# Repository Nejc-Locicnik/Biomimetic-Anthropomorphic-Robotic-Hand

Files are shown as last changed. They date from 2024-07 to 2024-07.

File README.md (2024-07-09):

# Biomimetic Anthropomorphic Robotic Hand

<div style="text-align: center;">
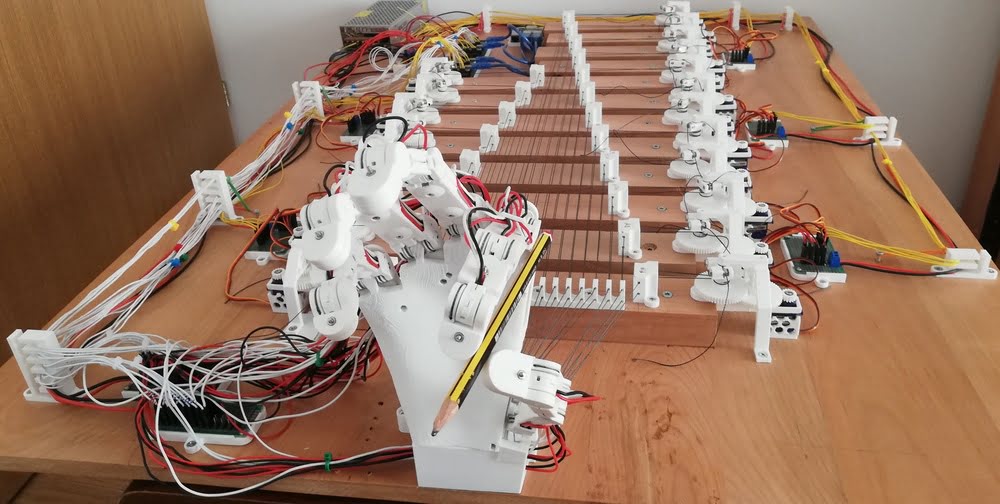
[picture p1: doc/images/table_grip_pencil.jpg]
Cool pic
  
</div>

## Introduction
This repository is a summarization of my diploma thesis, which can be fully read [here](/doc/Biomimetic_Anthropomorphic_Robotic_Hand_Thesis_SLO.pdf). 

The thesis is about designing and manufacturing a working prototype of a 3D printed cable-driven 20-DOF Biomimetic Anthropomorphic Robotic Hand. The main intent was to recreate appropriate hand proportions and joint motions with a simple and modular mechanical structure, which can easily be 3D printed.

## Actuator system

The original idea for moving the joints was to use small "micro" servos in the joints themselves, but I quickly figured that they simply don't provide enough torque to provide consistent motion to the joints (the hand would also become very heavy from the motors and extra cables required). I then pivoted towards cable-driven actuators, where the motors are moved out of the hand entirely. The base cable-pully system was taken from [here](https://www.youtube.com/watch?v=MxbX9iKGd6w&ab_channel=WillCogley). The issue with this system is that moving one joint moves the sequential joint in the opposite direction, I like to call this consequential movement.

I modified the original system by twisting/swapping the cables at specific spots to take advantage of consequential movement to make the finger motion more natural and easier to control. With this change we can actually move all 3 joints of a finger in the same direction with only 1 motor, sadly I figured this out too late and didn't want to modify the rest of the hand. 
The original system and the change are visualized in the following images. The motion is the same in both images (45° flex on each finger joint), but as we can see the final finger position is a lot different:

<div style="text-align: center;">
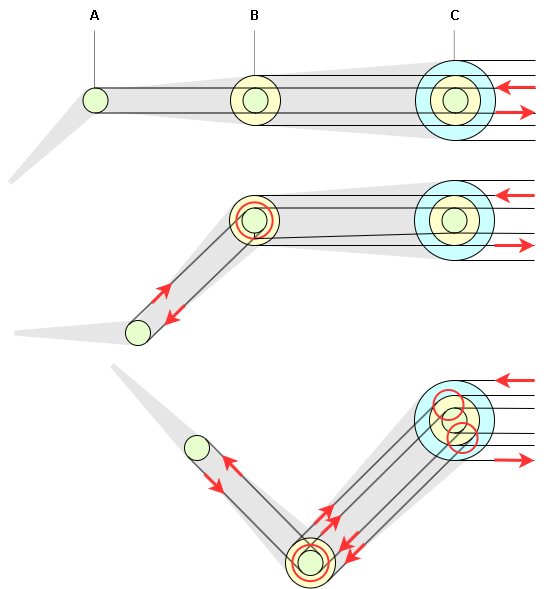
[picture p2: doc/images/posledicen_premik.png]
  
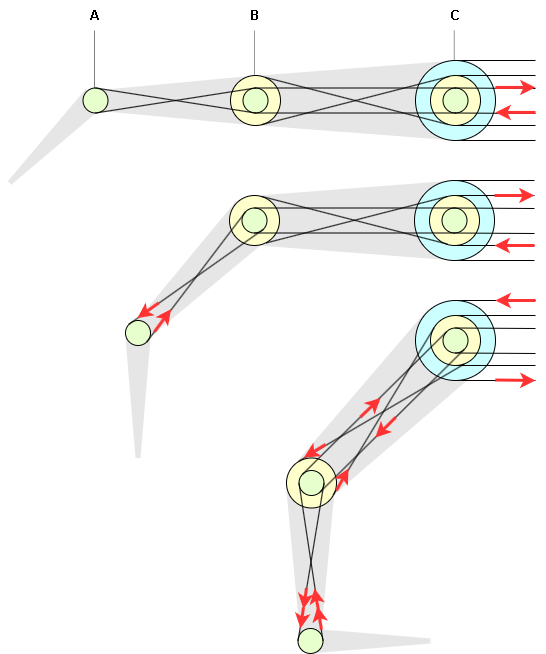
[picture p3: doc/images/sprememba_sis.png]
Modified system Modified system.
  
</div>

Check out the thesis if you are interested in consequential joint movement. I explain (with simple math/geometry) the cause, amount and direction of consequential movement. In my opinion this cable system modification is the most interesting bit of my thesis. 

## 3-D printed parts

All parts were modeled with SolidWorks (2022/2023) and 3D printed with Creality's Ender-5 (slicer used was CURA 5). Everything that could possibly be printed was printed (an extreme example: the joint axis were 3D printed). Most joints (DIP/PIP) are normal hinge joints, while the rest (MCP/CMC) are 2D joints that use a cross axis. All joints require a lot of small bearings.

A large majority of the project's time was spent on designing the robotic hand as I was referencing the actual anatomical structure of a human hand (proportions and the range of motion of each joint).

<div style="text-align: center;">
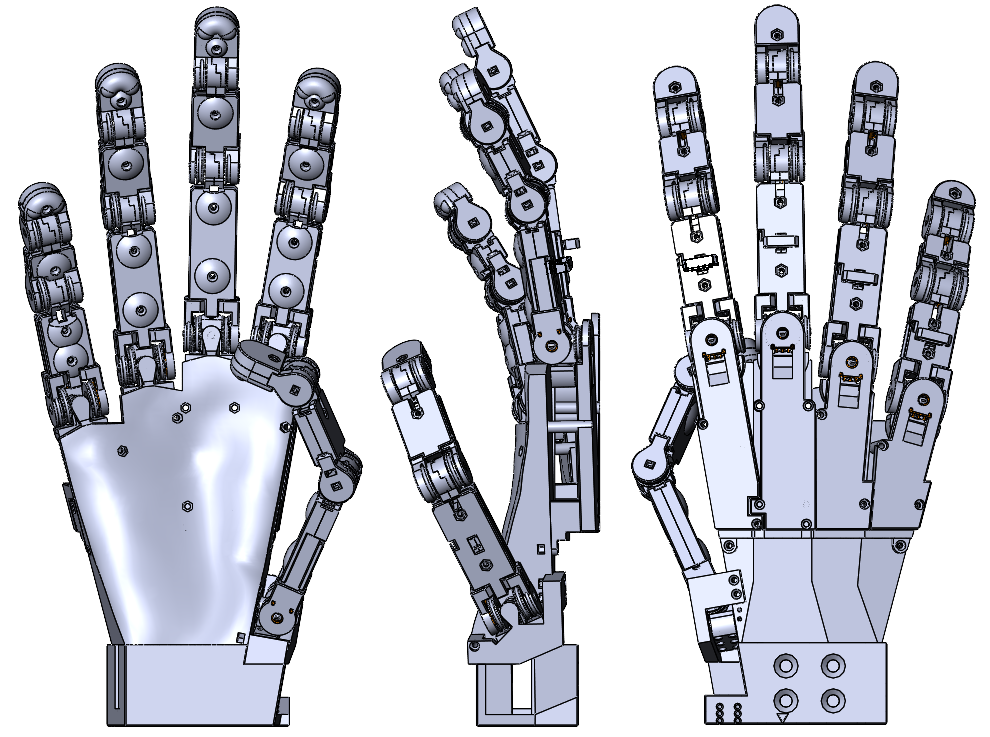
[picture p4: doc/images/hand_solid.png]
  
</div>

All parts required can be found in `/parts`.

## Code

The joints are split between 4 Arduino Nano's, which handle their PID control. The Arduino code includes potentiometer signal filtering and consequential joint movement error handling to prevent potential breaking (`\src\arduino\Nano_0*_dip\Nano_0*_dip.ino`). Each Arduino is then connected to a Raspberry Pi through USB (UART), so I could control the whole hand through a single input (`\src\raspberry\rpi_code.py`).

The code for each joint is organized into a HandJoint class (`\src\arduino\lib\HandJoint`), so there isn't a ton of repeated code for each joint.

## Result

The first thing that was tested was the operation viability of this prototype by manipulating the hand's fingers through commands on the Raspberry Pi. As seen in the animated GIF below the cable-pully system works great (in regard to moving the joints), the structure of the fingers is also strong enough that the first thing to break is usually the cable/string or rather the way they are attached might slip. The only issue is the finger oscillation. The cable-pully system allows some wiggle room, which when combined with consequential movement of joints and their PID control, makes the detailed control of fingers quite hard. Each joint is trying to correct itself, while another joint keeps disrupting its position. Additional processing of commands would be necessary, e.g. a command would determine the final position of each joint and would then be processed to only require minimal movement on each joint to reach said final position, rather than each joint attempting to reach the final position from the get-go. Note: this is sped-up, because of 3x frame-rate reduction.

<div style="text-align: center;">
  Finger oscillation
</div>

The second thing that was tested was the grasping ability of the hand's design. This test was done through manual movement of fingers. It followed the grasping taxonomy and is visualized below. Things that were found lacking was no movement in the palm under the little and ring finger (CMC joint) and the thumb orientation. These made grasping in some cases difficult as a correct angle for thumb opposition is required for a truly strong grasp. The other thing that was found was that the adaptability that the lateral movement of fingers offer, wasn't really necessary, specially in the middle and ring fingers. In this case it's possible to reduce structure complexity without reducing grasping capability.

<div style="text-align: center;">
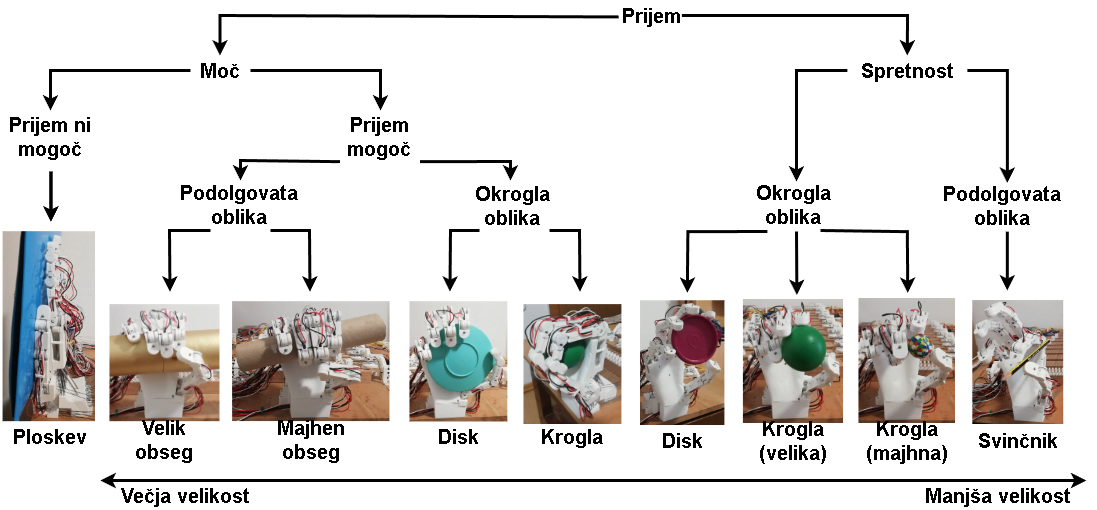
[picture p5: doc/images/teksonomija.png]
Grasping taxonomy
  
</div>

## Other comments

- stopped developing code part (kinematics, command processing), because I want to further refine the design first
- stopped further development in general, because a lacking use-case, if we are talking grasping ability in robotics, then we are better off with less complex task specific grippers and if we are talking about bionic hand prosthesis, there is currently too much extra stuff to fit into a reasonable forearm
- might reuse the cable-pully system and my modification for other biomimetic robotic projects, I find this field quite interesting

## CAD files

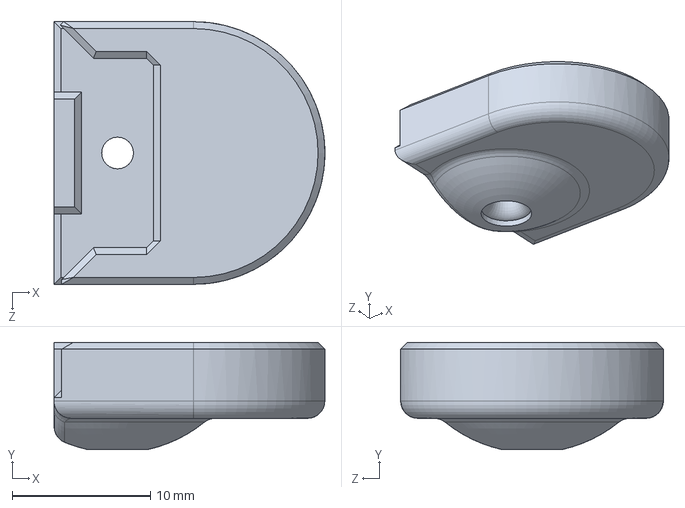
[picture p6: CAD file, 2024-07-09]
parts/MF_tip_top.SLDPRT
19.6 x 7.77 x 19.0 mm

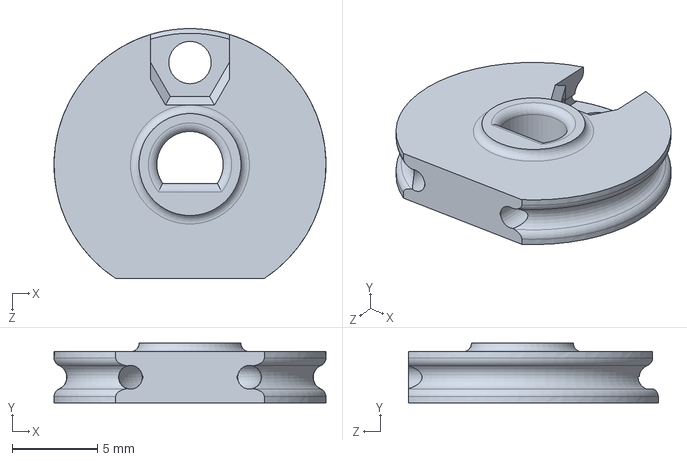
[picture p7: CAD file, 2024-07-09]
parts/MCP_rotation_pully.SLDPRT
16.0 x 3.50 x 14.7 mm

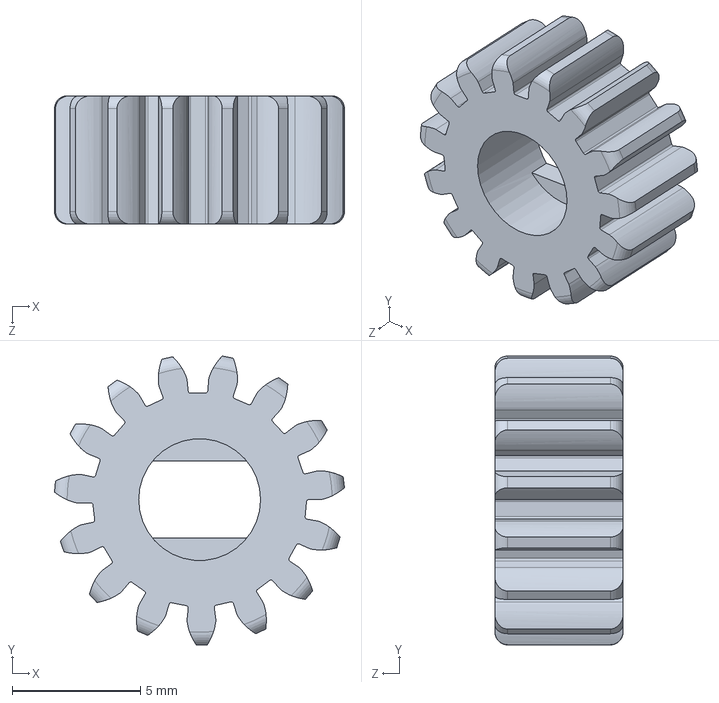
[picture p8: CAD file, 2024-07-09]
parts/motor_gear.SLDPRT
11.3 x 11.3 x 5.00 mm

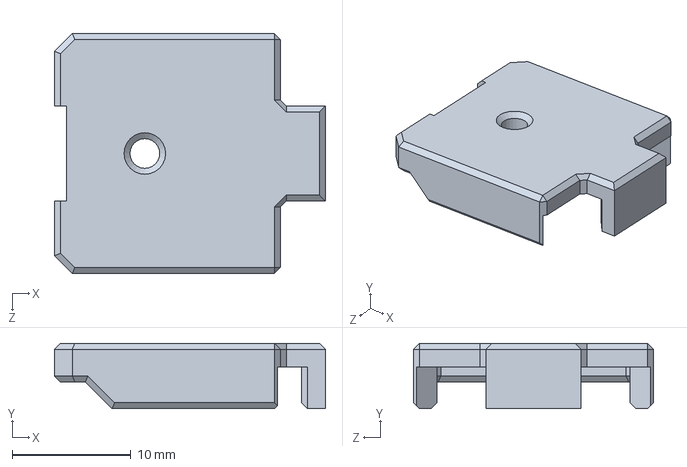
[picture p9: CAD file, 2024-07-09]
parts/RF_PIP_to_DIP_bottom_holder.SLDPRT
22.8 x 5.50 x 20.2 mm

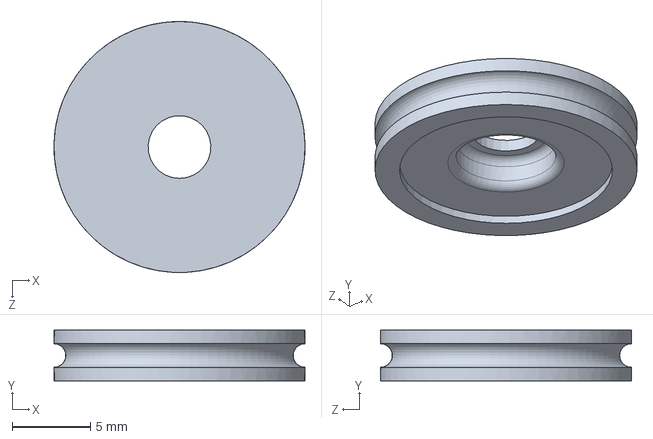
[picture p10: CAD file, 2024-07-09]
parts/pully1.SLDPRT
16.0 x 3.25 x 16.0 mm

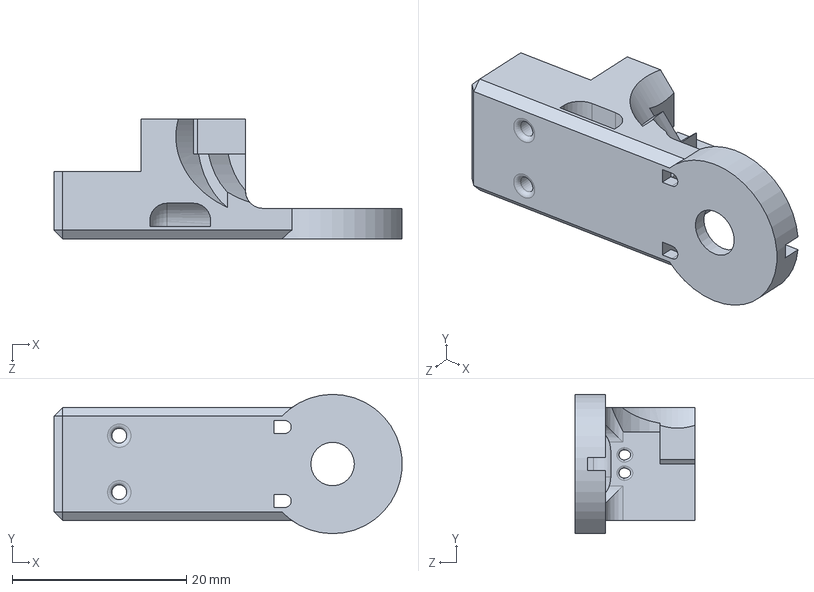
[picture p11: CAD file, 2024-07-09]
parts/IF_MCP_to_PIP_L_pot.SLDPRT
40.0 x 16.0 x 13.8 mm

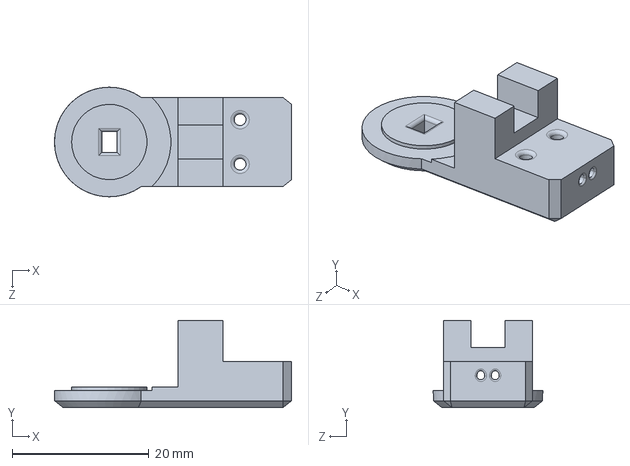
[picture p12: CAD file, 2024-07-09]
parts/RF_PIP_to_DIP_R.SLDPRT
34.6 x 12.8 x 16.0 mm

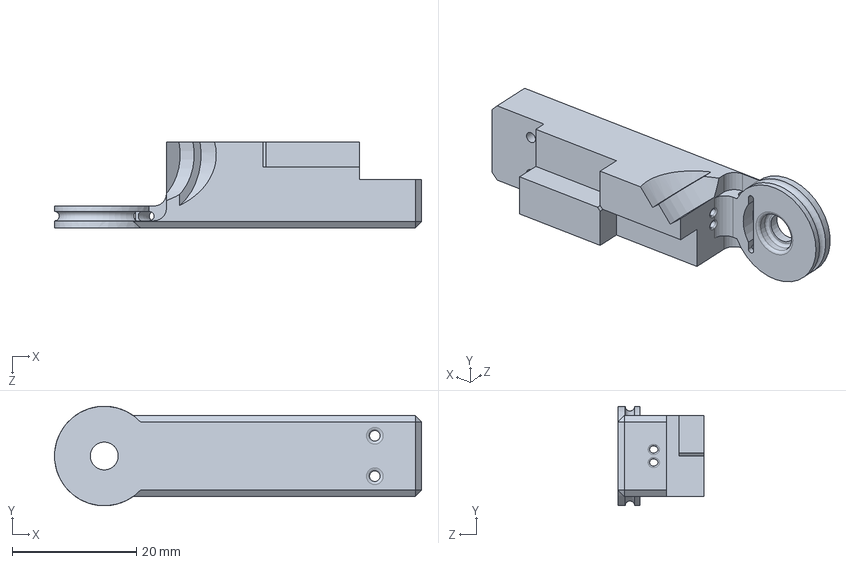
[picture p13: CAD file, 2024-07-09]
parts/RF_MCP_to_PIP_R.SLDPRT
59.0 x 16.0 x 13.8 mm

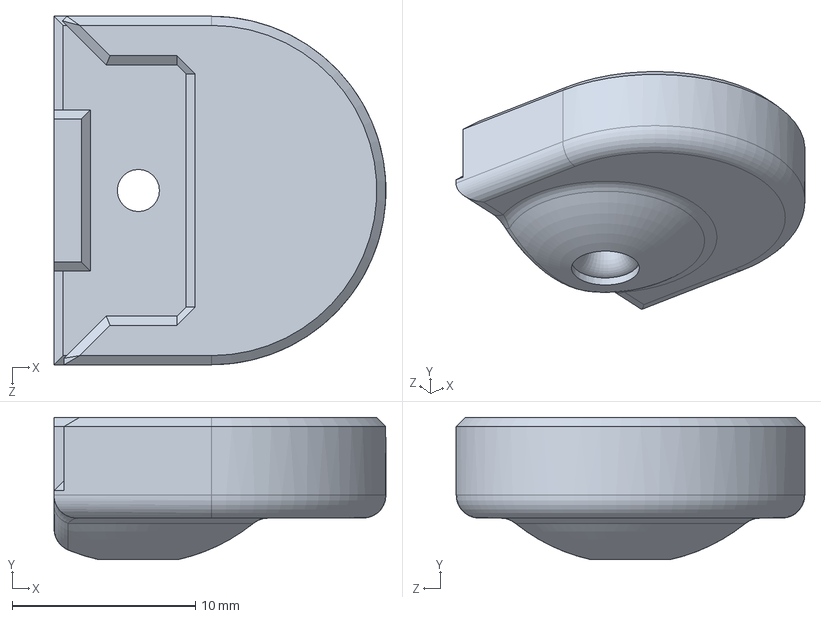
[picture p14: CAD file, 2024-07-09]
parts/MF_tip_bottom.SLDPRT
18.1 x 7.77 x 19.0 mm

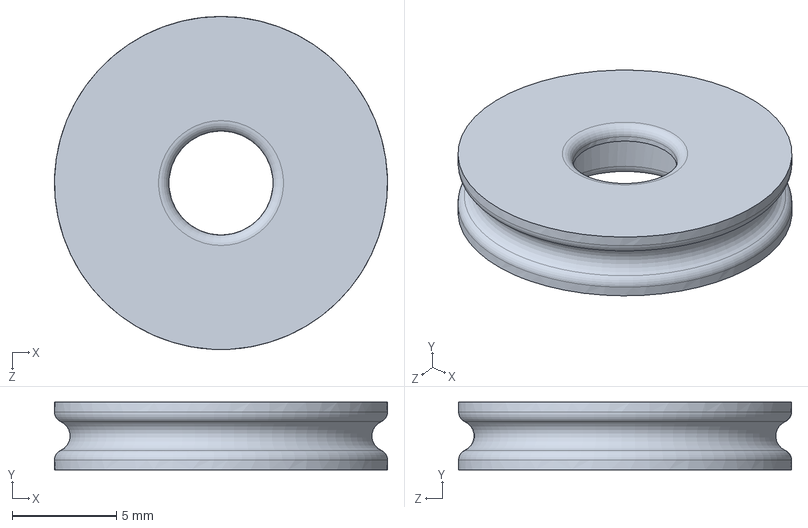
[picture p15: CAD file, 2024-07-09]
parts/7mm_pully.SLDPRT
16.0 x 3.25 x 16.0 mm

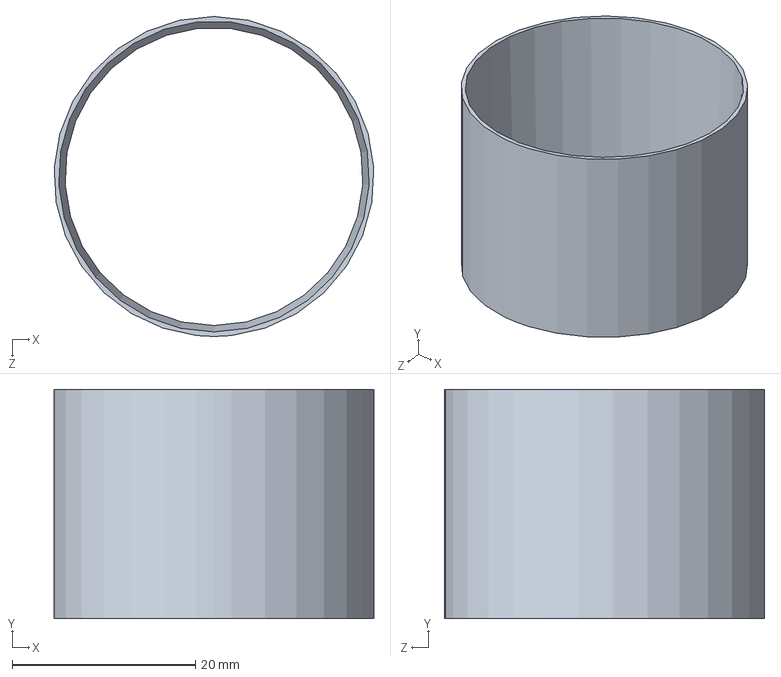
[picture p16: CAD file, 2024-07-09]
parts/nastavek_za_fotra.SLDPRT
34.8 x 25.0 x 34.9 mm

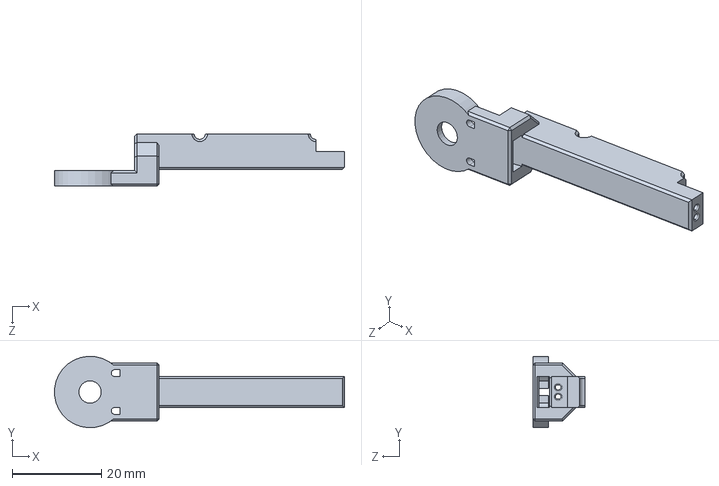
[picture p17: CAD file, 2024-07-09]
parts/proximal_L.SLDPRT
65.0 x 16.0 x 11.8 mm

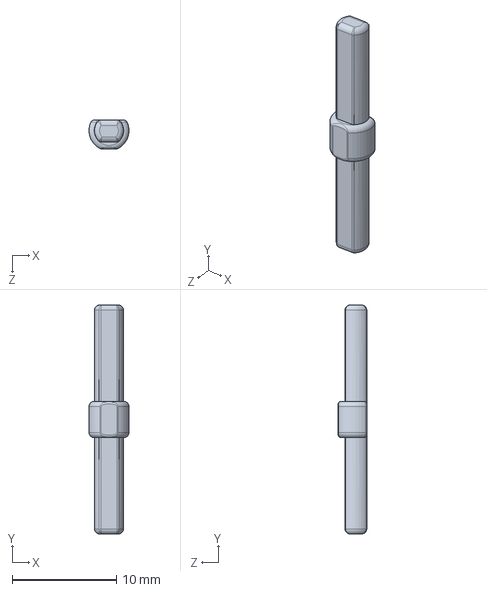
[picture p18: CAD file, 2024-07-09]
parts/PIP_pin.SLDPRT
3.84 x 22.0 x 2.75 mm

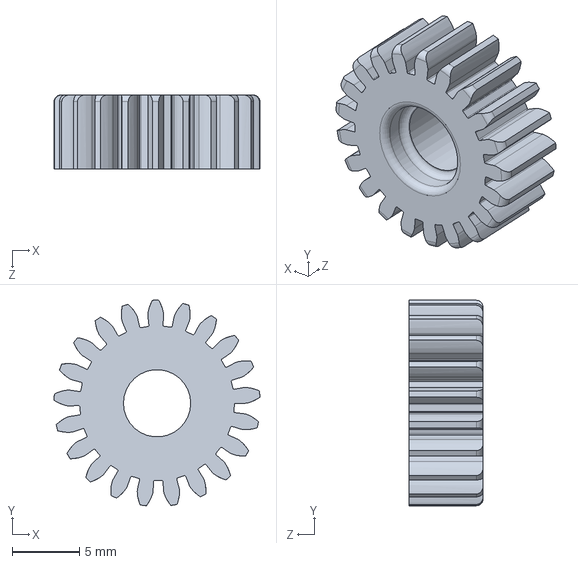
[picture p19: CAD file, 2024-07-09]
parts/small_gear_of_double.SLDPRT
15.3 x 15.3 x 5.50 mm

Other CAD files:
parts/RF_tip_top.SLDPRT
parts/RF_palm_back.SLDPRT
parts/LF_tip_top.SLDPRT
parts/act_pullyV2.SLDPRT
parts/DIP_pin.SLDPRT
parts/DIP_pot_L_holder.SLDPRT
parts/DIP_pot_R_holder.SLDPRT
parts/DIP_to_tip_L.SLDPRT
parts/DIP_to_tip_R.SLDPRT
parts/IF_MCP_to_PIP_R.SLDPRT
parts/IF_PIP_to_DIP_L.SLDPRT
parts/IF_PIP_to_DIP_R.SLDPRT
parts/IF_PIP_to_DIP_bottom_holder.SLDPRT
parts/IF_PIP_to_DIP_top_holder.SLDPRT
parts/IF_middle_R.STL.SLDPRT
parts/IF_palm_back.SLDPRT
parts/IF_proximal_bottom_holder.SLDPRT
parts/IF_tip_bottom.SLDPRT
parts/IF_tip_top.SLDPRT
parts/LF_MCP_to_PIP_L_pot.SLDPRT
parts/LF_MCP_to_PIP_R.SLDPRT
parts/LF_MCP_to_PIP_bottom_holder.SLDPRT
parts/LF_MCP_to_PIP_top_holder.SLDPRT
parts/LF_PIP_to_DIP_L.SLDPRT
parts/LF_PIP_to_DIP_R.SLDPRT
parts/LF_PIP_to_DIP_bottom_holder.SLDPRT
parts/LF_PIP_to_DIP_top_holder.SLDPRT
parts/LF_middle_L.STL.SLDPRT
parts/LF_middle_R.STL.SLDPRT
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

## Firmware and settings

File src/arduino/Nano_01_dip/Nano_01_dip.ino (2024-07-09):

#include <Servo.h>
#include <HandJoint.h>
#include <HandConstants.h>

// Communication variables
String spFIFO;
int sizeFIFO;
bool state;
unsigned long lastSend, tempTime; // runTime

HandJoint MCP_L(500, 912, 1);
HandJoint PIP_L(207, 998, 2);
HandJoint DIP_L(234, 920, 3);
HandJoint MCP_R(470, 874, 1);
HandJoint PIP_R(189, 959, 2);
HandJoint DIP_R(223, 927, 3);

Servo MCP_L_servo;
Servo PIP_L_servo;
Servo DIP_L_servo;
Servo MCP_R_servo;
Servo PIP_R_servo;
Servo DIP_R_servo;

void setup() {
    // put your setup code here, to run once:
    Serial.begin(9600);

    // Set state to pause
    state = false;
    sizeFIFO = 0;
    
    // Connecting servos to PWM pins and set min and max values
    MCP_L_servo.attach(MCP_L_SERVO, 500, 2500);
    PIP_L_servo.attach(PIP_L_SERVO, 500, 2500);
    DIP_L_servo.attach(DIP_L_SERVO, 500, 2500);
    MCP_R_servo.attach(MCP_R_SERVO, 500, 2500);
    PIP_R_servo.attach(PIP_R_SERVO, 500, 2500);
    DIP_R_servo.attach(DIP_R_SERVO, 500, 2500);

    // Read initial joint positions and init filtering arrays
    MCP_L.initFiltering(analogRead(MCP_L_POTENTIOMETER));
    PIP_L.initFiltering(analogRead(PIP_L_POTENTIOMETER));
    DIP_L.initFiltering(analogRead(DIP_L_POTENTIOMETER));
    MCP_R.initFiltering(analogRead(MCP_R_POTENTIOMETER));
    PIP_R.initFiltering(analogRead(PIP_R_POTENTIOMETER));
    DIP_R.initFiltering(analogRead(DIP_R_POTENTIOMETER));

    // Initial joint positions are whatever the current position is, because we don't want anything to move on startup
    MCP_L.updateSetpoint(MCP_L.joint_position);
    PIP_L.updateSetpoint(PIP_L.joint_position);
    DIP_L.updateSetpoint(DIP_L.joint_position);
    MCP_R.updateSetpoint(MCP_R.joint_position);
    PIP_R.updateSetpoint(PIP_R.joint_position);
    DIP_R.updateSetpoint(DIP_R.joint_position); 

    // Invert servo rotation on PIP and DIP joints, because the strings are twisted
    PIP_L.invertServoRotation();
    DIP_L.invertServoRotation();
    PIP_R.invertServoRotation();
    DIP_R.invertServoRotation();

    // Don't allow motor movement initially
    stopAllMotors();
}

void loop() {
    while (true) {
        //runTime = micros();

        // Update potentiometer values
        MCP_L.updateJointPosition(analogRead(MCP_L_POTENTIOMETER));
        PIP_L.updateJointPosition(analogRead(PIP_L_POTENTIOMETER));
        DIP_L.updateJointPosition(analogRead(DIP_L_POTENTIOMETER));
        MCP_R.updateJointPosition(analogRead(MCP_R_POTENTIOMETER));
        PIP_R.updateJointPosition(analogRead(PIP_R_POTENTIOMETER));
        DIP_R.updateJointPosition(analogRead(DIP_R_POTENTIOMETER));

        // Periodicaly send data, limited to set period to not spam serial connection which can cause problems
        tempTime = micros();
        if (tempTime - lastSend > 500000) {
            sendStateData();
            //plot();
            lastSend = tempTime;
        }

        // Check for new instructions
        checkForInstructions();

        // If sp buffer isnt empty, update the next SP
        if (sizeFIFO > 0) {
            updateJointSP();
        }

        // Break the while loop if state is Active, else if state is Stop, stop all motors
        if (state) {
            break;          
        } else {
            stopAllMotors();
        }
    }

    // Calculate PID value and move motors
    //Serial.println(DIP_L.regulateJoint(1, 1));
    /*
    DIP_L.regulateJoint(1, 1);
    PIP_L.regulateJoint(1, DIP_L.joint_movement_available);
    DIP_R.regulateJoint(1, 1);
    PIP_R.regulateJoint(1, DIP_R.joint_movement_available);*/
    
    DIP_L_servo.writeMicroseconds(DIP_L.regulateJoint(1, 1));
    PIP_L_servo.writeMicroseconds(PIP_L.regulateJoint(1, DIP_L.joint_movement_available));
    MCP_L_servo.writeMicroseconds(MCP_L.regulateJoint(PIP_L.joint_movement_available, DIP_L.joint_movement_available));
    
    DIP_R_servo.writeMicroseconds(DIP_R.regulateJoint(1, 1));
    PIP_R_servo.writeMicroseconds(PIP_R.regulateJoint(1, DIP_R.joint_movement_available));
    MCP_R_servo.writeMicroseconds(MCP_R.regulateJoint(PIP_R.joint_movement_available, DIP_R.joint_movement_available));
    
    //while (micros() - runTime < 100000) {}
    ///delay(500);
}

// check serial connection for new commands, current available commands are W, A, S, C;
void checkForInstructions() {
    String input;

    if (Serial.available()) {
        input = Serial.readString();

        switch (input[0]) {
            case 'W': // update set-point values
                sizeFIFO += (int)(input[1] - 48); // number 0 has ASCII code 48, so we reduce the value by 48 to get proper integers
                spFIFO += input.substring(2, (int)(input[1] - 48) * 4 + 2); // second index until the end of msg, can't put -1 because serial adds a sign at the end
                break;
            case 'A': // change state to active
                state = true;
                break;
            case 'S': // change state to stop
                state = false;
                break;
            /*
            case 'C': // clear set-point FIFO
                sizeFIFO = 0;
                spFIFO = "";
                break;*/
            // potentially add additional commands, such as adjusting PID constants
        }
        //Serial.println("Recieved!");
    }
}

// update the first joint set-point (SP value) in the FIFO
void updateJointSP() {
    // update first sp in buffer before deleting it
    char sp_id = spFIFO[0];
    int sp_val = spFIFO.substring(1, 4).toInt();
    
    switch (sp_id) {
        case MCP_L_ID:
            MCP_L.updateSetpoint(sp_val);
        case PIP_L_ID:
            PIP_L.updateSetpoint(sp_val);
        case DIP_L_ID:
            DIP_L.updateSetpoint(sp_val);        
        case MCP_R_ID:
            MCP_R.updateSetpoint(sp_val);
        case PIP_R_ID:
            PIP_R.updateSetpoint(sp_val);
        case DIP_R_ID:
            DIP_R.updateSetpoint(sp_val);      
    }

    // delete the updated joint setpoint
    spFIFO = spFIFO.substring(4, -1);
    sizeFIFO -= 1;
}

void stopAllMotors() {
    MCP_L_servo.writeMicroseconds(1500);
    PIP_L_servo.writeMicroseconds(1500);
    DIP_L_servo.writeMicroseconds(1500);
    MCP_R_servo.writeMicroseconds(1500);
    PIP_R_servo.writeMicroseconds(1500);
    DIP_R_servo.writeMicroseconds(1500);
}

void plot() {
    Serial.print("static1:");
    Serial.print(650);
    Serial.print("\t");
    Serial.print("static2:");
    Serial.print(450);
    Serial.print("\t");
    Serial.print("Little MCP:");
    Serial.print(MCP_L.joint_position);
    Serial.print("\t");
    Serial.print("Little PIP:");
    Serial.print(PIP_L.joint_position);
    Serial.print("\t");
    Serial.print("Little DIP:");
    Serial.print(DIP_L.joint_position);
    Serial.print("\t");
    Serial.print("Ring MCP:");
    Serial.print(MCP_R.joint_position);
    Serial.print("\t");
    Serial.print("Ring PIP:");
    Serial.print(PIP_R.joint_position);
    Serial.print("\t");
    Serial.print("Ring DIP:");
    Serial.print(DIP_R.joint_position);
    Serial.println();
}

void sendStateData() {
    // format: {{state:1},{A:999,B:999,C:999,D:999,Z:999}}
    Serial.print("{{id:1},{state:");
    Serial.print(state);
    Serial.print("},{A:");
    Serial.print(MCP_L.joint_position);
    Serial.print(",B:");
    Serial.print(DIP_L.joint_position);
    Serial.print(",C:");
    Serial.print(PIP_L.joint_position);
    Serial.print(",E:");
    Serial.print(MCP_R.joint_position);
    Serial.print(",F:");
    Serial.print(DIP_R.joint_position);
    Serial.print(",G:");
    Serial.print(PIP_R.joint_position);
    Serial.print("}}\n");
}

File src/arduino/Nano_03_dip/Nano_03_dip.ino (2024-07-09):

#include <Servo.h>
#include <HandJoint.h>
#include <HandConstants.h>

// Communication variables
String spFIFO;
int sizeFIFO;
bool state;
unsigned long lastSend, tempTime; // runTime

HandJoint MCP_M(478, 897, 1);
HandJoint PIP_M(198, 967, 2);
HandJoint DIP_M(210, 951, 3);
HandJoint MCP_I(487, 902, 1);
HandJoint PIP_I(172, 941, 2);
HandJoint DIP_I(243, 900, 3);

Servo MCP_M_servo;
Servo PIP_M_servo;
Servo DIP_M_servo;
Servo MCP_I_servo;
Servo PIP_I_servo;
Servo DIP_I_servo;

void setup() {
    // put your setup code here, to run once:
    Serial.begin(9600);

    // Set state to pause
    state = false;
    sizeFIFO = 0;

    // Connecting servos to PWM pins and set min and max values
    MCP_M_servo.attach(MCP_M_SERVO, 500, 2500);
    PIP_M_servo.attach(PIP_M_SERVO, 500, 2500);
    DIP_M_servo.attach(DIP_M_SERVO, 500, 2500);
    MCP_I_servo.attach(MCP_I_SERVO, 500, 2500);
    PIP_I_servo.attach(PIP_I_SERVO, 500, 2500);
    DIP_I_servo.attach(DIP_I_SERVO, 500, 2500);

    // Read initial joint positions and init filtering arrays
    MCP_M.initFiltering(analogRead(MCP_M_POTENTIOMETER));
    PIP_M.initFiltering(analogRead(PIP_M_POTENTIOMETER));
    DIP_M.initFiltering(analogRead(DIP_M_POTENTIOMETER));
    MCP_I.initFiltering(analogRead(MCP_I_POTENTIOMETER));
    PIP_I.initFiltering(analogRead(PIP_I_POTENTIOMETER));
    DIP_I.initFiltering(analogRead(DIP_I_POTENTIOMETER));
    
    // Initial joint positions are whatever the current position is, because we don't want anything to move on startup
    MCP_M.updateSetpoint(MCP_M.joint_position);
    PIP_M.updateSetpoint(PIP_M.joint_position);
    DIP_M.updateSetpoint(DIP_M.joint_position);
    MCP_I.updateSetpoint(MCP_I.joint_position);
    PIP_I.updateSetpoint(PIP_I.joint_position);
    DIP_I.updateSetpoint(DIP_I.joint_position);

    // Invert servo rotation on PIP and DIP joints, because the strings are twisted
    PIP_M.invertServoRotation();
    DIP_M.invertServoRotation();
    PIP_I.invertServoRotation();
    DIP_I.invertServoRotation();

    // Don't allow motor movement initially
    stopAllMotors();
}

void loop() {
    while (true) {
        //runTime = micros();

        // Update potentiometer values
        MCP_M.updateJointPosition(analogRead(MCP_M_POTENTIOMETER));
        PIP_M.updateJointPosition(analogRead(PIP_M_POTENTIOMETER));
        DIP_M.updateJointPosition(analogRead(DIP_M_POTENTIOMETER));
        MCP_I.updateJointPosition(analogRead(MCP_I_POTENTIOMETER));
        PIP_I.updateJointPosition(analogRead(PIP_I_POTENTIOMETER));
        DIP_I.updateJointPosition(analogRead(DIP_I_POTENTIOMETER));

        // Periodicaly send data, limited to set period to not spam serial connection which can cause problems
        tempTime = micros();
        if (tempTime - lastSend > 500000) {
            sendStateData();
            //plot();
            lastSend = tempTime;
        }

        // Check for new instructions
        checkForInstructions();

        // If sp buffer isn't empty, update the next SP
        if (sizeFIFO > 0) {
            updateJointSP();
        }

        // Break the while loop if state is Active, else if state is Stop, stop all motors
        if (state) {
            break;          
        } else {
            stopAllMotors();
        }
    }

    //tmp
    DIP_M.regulateJoint(1, 1);
    PIP_M.regulateJoint(1, DIP_M.joint_movement_available);
    DIP_I.regulateJoint(1, 1);
    PIP_I.regulateJoint(1, DIP_I.joint_movement_available);
    
    // Regulate joints based on the error in positions
    //DIP_M_servo.writeMicroseconds(DIP_M.regulateJoint(1, 1));
    //PIP_M_servo.writeMicroseconds(PIP_M.regulateJoint(1, DIP_M.joint_movement_available)); 
    MCP_M_servo.writeMicroseconds(MCP_M.regulateJoint(PIP_M.joint_movement_available, DIP_M.joint_movement_available));

    //DIP_I_servo.writeMicroseconds(DIP_I.regulateJoint(1, 1));
    //PIP_I_servo.writeMicroseconds(PIP_I.regulateJoint(1, DIP_I.joint_movement_available));
    MCP_I_servo.writeMicroseconds(MCP_I.regulateJoint(PIP_I.joint_movement_available, DIP_I.joint_movement_available));
    
    //while (micros() - runTime < 100000) {}
}

// check serial connection for new commands, current available commands are W, A, S;
void checkForInstructions() {
    String input;

    if (Serial.available()) {
        input = Serial.readString();
        switch (input[0]) {
            case 'W': // update set-point values
                sizeFIFO += (int)(input[1] - 48); // number 0 has ASCII code 48
                // second index until the end of msg, 
                // can't put -1 because serial adds a sign at the end
                spFIFO += input.substring(2, (int)(input[1] - 48) * 4 + 2); 
                break;
            case 'A': // change state to active
                state = true;
                break;
            case 'S': // change state to stop
                state = false;
                break;
            // potentially add additional commands
        }
        //Serial.println("Recieved!");
    }
}

// update the first joint set-point (SP value) in the FIFO
void updateJointSP() {
    // update first sp in buffer before deleting it
    char sp_id = spFIFO[0];
    int sp_val = spFIFO.substring(1, 4).toInt();
    
    switch (sp_id) {
        case MCP_M_ID:
            MCP_M.updateSetpoint(sp_val);
        case PIP_M_ID:
            PIP_M.updateSetpoint(sp_val);
        case DIP_M_ID:
            DIP_M.updateSetpoint(sp_val);        
        case MCP_I_ID:
            MCP_I.updateSetpoint(sp_val);
        case PIP_I_ID:
            PIP_I.updateSetpoint(sp_val);
        case DIP_I_ID:
            DIP_I.updateSetpoint(sp_val);      
    }

    // delete the updated joint setpoint
    spFIFO = spFIFO.substring(4, -1);
    sizeFIFO -= 1;
}

void stopAllMotors() {
    MCP_M_servo.writeMicroseconds(1500);
    PIP_M_servo.writeMicroseconds(1500);
    DIP_M_servo.writeMicroseconds(1500);
    MCP_I_servo.writeMicroseconds(1500);
    PIP_I_servo.writeMicroseconds(1500);
    DIP_I_servo.writeMicroseconds(1500);
}

void plot() {
    Serial.print("static1:");
    Serial.print(650);
    Serial.print("\t");
    Serial.print("static2:");
    Serial.print(450);
    Serial.print("\t");
    Serial.print("Middle MCP:");
    Serial.print(MCP_M.joint_position);
    Serial.print("\t");
    Serial.print("Middle PIP:");
    Serial.print(PIP_M.joint_position);
    Serial.print("\t");
    Serial.print("Middle DIP:");
    Serial.print(DIP_M.joint_position);
    Serial.print("\t");
    Serial.print("Index MCP:");
    Serial.print(MCP_I.joint_position);
    Serial.print("\t");
    Serial.print("Index PIP:");
    Serial.print(PIP_I.joint_position);
    Serial.print("\t");
    Serial.print("Index DIP:");
    Serial.print(DIP_I.joint_position);
    Serial.println();
}
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
